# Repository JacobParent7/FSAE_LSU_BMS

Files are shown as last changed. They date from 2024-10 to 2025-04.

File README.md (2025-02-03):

# Motherboard
SENTRY



# Goal

Develop a distributed Battery Management System (BMS) for LSU FSAE's electric accumulator to be used in 2026 competition, targeting completion by May, 2025. All hardware and firmware development will be documented in this repository.

# Contact Info
### Motherboard Design
- Jacob Parent - jparen6@lsu.edu
### Daughterboard Design
- Parth Mistry - pmistr2@lsu.edu
- Modhy Alsahood - malsah1@lsu.edu

# FSAE BMS Design Log

## System Level Description 
BMS - MOBO drawio

## Orion BMS Thermistor Expansion Reverse Engineering
Blank diagram (1)

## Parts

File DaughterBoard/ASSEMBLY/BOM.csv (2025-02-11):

Reference | Value | Footprint | JLC PCB Part #
C201 | 10nF | GCM188R72A103KA37J:CAPC1608X90N | C2167085
C202,C208 | 0.1uF | GCM155R71A104KA55D:CAP_GCM15_1p05X0p55X0p55_MUR-L | C161163
C203,C204,C205,C207 | 1uF | C0603C105K8RACAUTO:CAPC18095_95N_KEM-L | C29936
C206 | 4.7uF | C2012X7R1A475M125AC:CAP_2012_TDK-L | C277499
C301,C302,C303,C304,C305,C306,C307,C308,C309,C310,C311,C312,C313,C314,C315,C316,C317,C318,C319,C320,C321,C322,C323,C324,C325,C326,C327,C328,C329,C330 | 0.47uF | GCM188R71C474KA55D:G-188_MUR-L | C161214
C601 | 0.22uF | GCM31MR72A224KA37L:G-31_MUR-L | C161277
C701,C702,C707,C708 | 2200pF | 1206J2K00222KXR (1):CAPC3216X160N | C107194
C703,C704,C705,C706 | 220pF | CL10B221JB8NNNC:CAP_CL10_SAM-L | C107081
D701,D702 | 24V | Package_TO_SOT_SMD:SOT-23 | C314266
F301,F302,F303,F304,F305,F306,F307,F308,F309,F310,F311,F323,F324,F325,F326 | 0438.250WRA | Fuse:Fuse_0603_1608Metric | C151137
F312,F313,F314,F315,F316,F317,F318,F319,F320,F321,F322,F327,F328,F329,F330 | 0686F1000-01 | 0686F1000-01:FUSC1608X60N | C136329
FL701,FL702 | 470uH | KiCad:744242471 | C488250
Q601 | ZXTN4004KTC | ZXTN4004KTC:ZXTN4004KTC | C157603
R201 | 30 | ERJ-3EKF30R0V:RC0603N_PAN-L | C403150
R301,R302,R303,R304,R305,R306,R307,R308,R309,R310,R311,R323,R324,R325,R326 | 7.5 | Resistor_SMD:R_1812_4532Metric | C5204035
R312,R313,R314,R315,R316,R317,R318,R319,R320,R321,R322,R327,R328,R329,R330 | 100 | Resistor_SMD:R_0603_1608Metric | C5123580
R601 | 100 | CRCW2010100RFKEF:RES_CRCW_2010-L | C305269
R602 | 200 | Resistor_SMD:R_2512_6332Metric | C2935248
R701,R702,R705,R706,R709,R710,R713,R714,R715,R716,R721,R722 | 0 | CRCW08050000Z0EAHP:RES_CRCW_0805_VIS-L | C844811
R703,R704,R719,R720 | 0 | RC0603JR-070RL:RC0603N_YAG-L | C95177
R707,R708,R717,R718 | 51 | CRCW060351R0JNEA:RC0603N_VIS-L | C844178
R711,R712 | 1k | ERJ-3EKF1001V:RC0603N_PAN-L | C2907002
U201 | BQ79614PAPRQ1 | BQ79614:QFP_4PAPRQ1_TEX-L | C3682338

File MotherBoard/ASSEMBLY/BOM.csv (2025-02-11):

Value | Reference | Footprint | JLCPCB Part #
100n | C203,C204,C206,C208,C210,C213,C215,C405,C406,C415,C416,C417,C418,C611,C612,C616,C617 | Capacitor_SMD:C_0402_1005Metric | C1525
100p | C503,C504,C505,C506 | Capacitor_SMD:C_0402_1005Metric | C1546
20p | C601,C602,C605,C606,C607,C608,C609,C610 | Capacitor_SMD:C_0402_1005Metric | C1554
RED | D501 | LED_SMD:LED_0603_1608Metric | C2286
Q_NMOS_GDS | Q704,Q705,Q706,Q708 | Package_TO_SOT_SMD:TO-263-2 | C2613
STM32F205RBTx | U201 | Package_QFP:LQFP-64_10x10mm_P0.5mm | C8364
1k | R201,R409,R410,R501 | Resistor_SMD:R_0402_1005Metric | C11702
Fuse | F701,F702,F703,F704 | Fuse:Fuse_1812_4532Metric | C12559
10u | C701,C702,C703,C704 | Capacitor_SMD:C_1206_3216Metric | C13585
16 Mhz | Y201 | Crystal:Crystal_SMD_3225-4Pin_3.2x2.5mm | C13738
0R | R203 | Resistor_SMD:R_0402_1005Metric | C17168
0R | R516,R517,R518,R519,R524,R525,R526,R527,R613,R614,R615,R616,R617,R618 | Resistor_SMD:R_0805_2012Metric | C17477
51 | R510,R511,R512,R513 | Resistor_SMD:R_1206_3216Metric | C18019
10u | C201,C216,C614,C619 | Capacitor_SMD:C_0603_1608Metric | C19702
220n | C507,C513 | Capacitor_SMD:C_0603_1608Metric | C21120
10n | L201 | Inductor_SMD:L_0402_1005Metric | C21585
D_Schottky | D405,D406 | Diode_SMD:D_SMA | C22452
499 | R502,R503,R504,R505 | Resistor_SMD:R_0603_1608Metric | C23065
22R | R204,R205,R206,R207,R210 | Resistor_SMD:R_0402_1005Metric | C25092
0R | R211 | Resistor_SMD:R_2512_6332Metric | C25469
100k | R402,R403,R405,R506,R515,R707,R708,R709,R712 | Resistor_SMD:R_0402_1005Metric | C25741
33k | R401,R404 | Resistor_SMD:R_0402_1005Metric | C25779
2.2k | R305 | Resistor_SMD:R_1206_3216Metric | C26038
2200p | C509,C510,C511,C512 | Capacitor_SMD:C_0805_2012Metric | C28260
1u | C409,C410,C411,C412,C413,C414 | Capacitor_SMD:C_0805_2012Metric | C28323
1u | C212,C214,C301,C613,C615,C618,C620 | Capacitor_SMD:C_0402_1005Metric | C29266
4.7u | C403,C404 | Capacitor_SMD:C_1206_3216Metric | C29823
22.1k | R406,R408 | Resistor_SMD:R_0402_1005Metric | C43473
22u | C419,C420,C421,C422,C423,C424 | Capacitor_SMD:C_0805_2012Metric | C45783
D_Zener | D401,D402 | Diode_SMD:D_SOD-323 | C46279
220n | C508 | Capacitor_SMD:C_0402_1005Metric | C47129
D_TVS | D201,D203,D204,D205,D206,D207,D208,D209,D301,D302,D303,D304,D305 | Diode_SMD:D_SOD-323 | C51450
10n | C211,C401,C402,C501,C502 | Capacitor_SMD:C_0402_1005Metric | C60133
2u2 | C207,C209 | Capacitor_SMD:C_0603_1608Metric | C99228
DM3AT-SF-PEJM5_40_ | J202 | SDIO:SD_CARD | C114218
100u | C407,C408 | Capacitor_SMD:CP_Elec_6.3x5.8 | C128464
10u | L403,L404 | Inductor_SMD:L_Sunlord_MWSA0603S | C132141
10p | C202,C205 | Capacitor_SMD:C_0402_1005Metric | C161520
3A | F401,F402 | Fuse:Fuse_1206_3216Metric | C182445
60.4 | R609,R610,R611,R612 | Resistor_SMD:R_1210_3225Metric | C230306
Fuse | F301,F302 | Fuse:Fuse_0805_2012Metric | C269104
4.7n | C603,C604 | Capacitor_SMD:C_0402_1005Metric | C281757
D_TVS | D403,D404,D407,D408 | Diode_SMD:D_SOD-123 | C353317
0R | R603,R604,R605,R606 | Resistor_SMD:R_1206_3216Metric | C473612
WE-SLM | L501,L502 | WE-SLM:WE-SLM | C488250
GREEN | D202,D409,D410 | LED_SMD:LED_0603_1608Metric | C511604
D_TVS | D502,D503,D504,D505 | Diode_SMD:D_SOD-323 | C668923
BQ79600PWRQ1 | IC501 | BQ79600:BQ79600 | C2869947
22R | R301,R302,R303,R304 | Resistor_SMD:R_1206_3216Metric | C2907457
10k | R202,R208,R209,R212,R507,R508,R509,R514,R601,R602,R607,R608,R701,R702,R703,R704,R705,R706,R710,R711 | Resistor_SMD:R_0402_1005Metric | C2930027
162k | R407 | Resistor_SMD:R_0402_1005Metric | C2998128
LMR51430 | U401,U402 | Package_TO_SOT_SMD:SOT-23-6 | C5210749
1.2u | L401,L402 | Inductor_SMD:L_Chilisin_BMRA00050530 | C5296375
PTCAN1462DRQ1 | U601,U602 | CAN1462:CAN1462 | C7399456
Q_NPN_BEC | Q701,Q702,Q703,Q707 | Package_TO_SOT_SMD:SOT-23 | C7420353
40V | D701,D702,D703,D704 | Diode_SMD:D_SOD-123 | C19077418

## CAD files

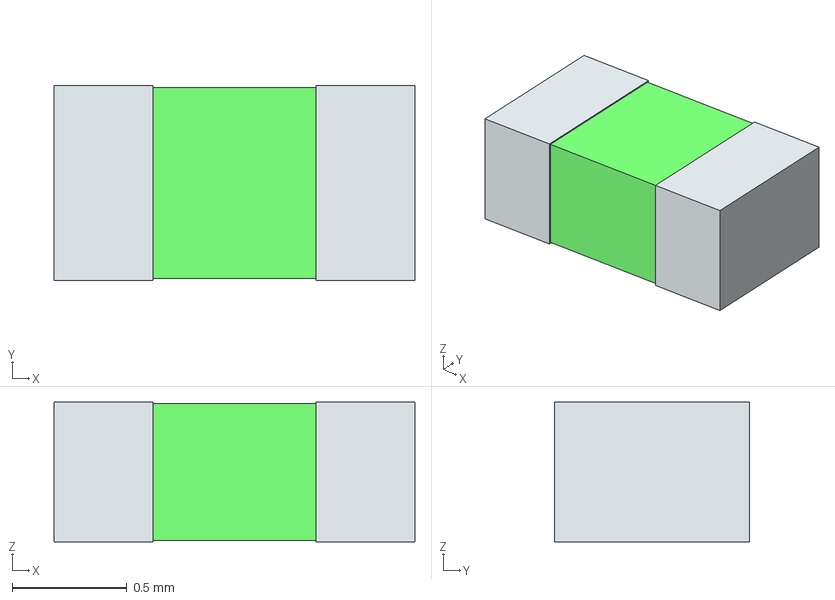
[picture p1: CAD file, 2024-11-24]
DaughterBoard/symbol-libs/models/0438.250WRASTEP/0438.250WRA.stp
1.57 x 0.85 x 0.61 mm
term1
term2

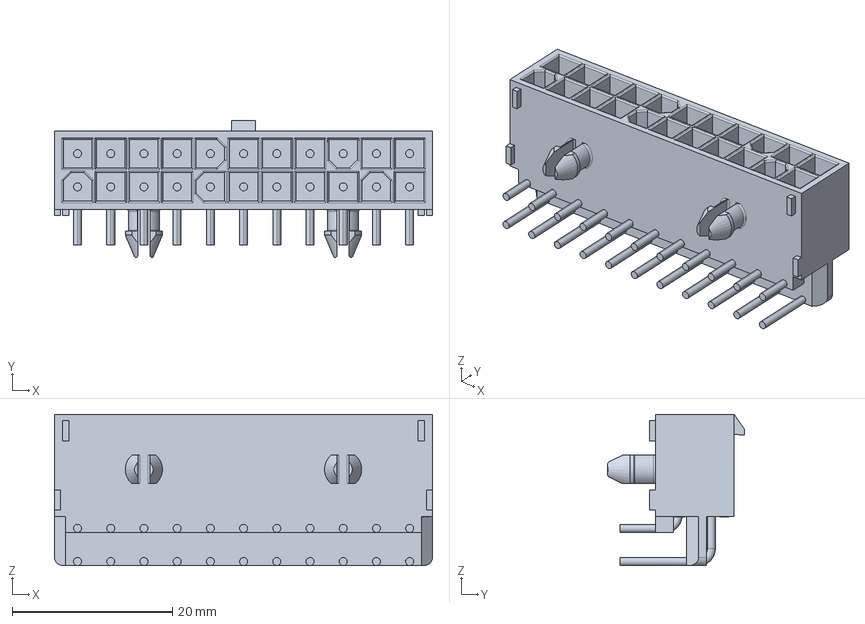
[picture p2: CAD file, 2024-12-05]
DaughterBoard/symbol-libs/models/c-1-794107-0-b-3d.stp
47.1 x 17.1 x 18.8 mm

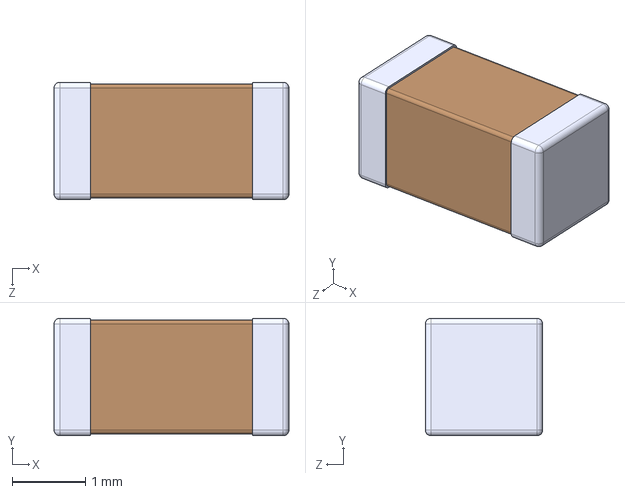
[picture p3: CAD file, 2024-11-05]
DaughterBoard/symbol-libs/symbols/1206J2K00222KXR (1)/1206J2K00222KXR.step
3.20 x 1.60 x 1.60 mm

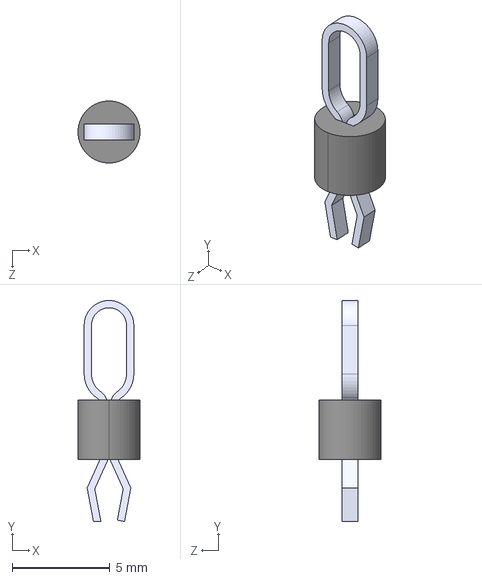
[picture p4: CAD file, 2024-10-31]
DaughterBoard/symbol-libs/symbols/5011 (1)/5011.step
3.17 x 11.3 x 3.17 mm

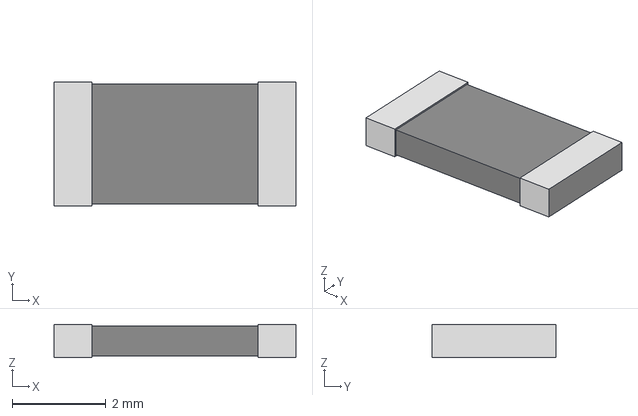
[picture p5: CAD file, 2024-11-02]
DaughterBoard/symbol-libs/symbols/CRCW2010100RFKEF/CRCW2010100RFKEF.step
5.16 x 2.64 x 0.711 mm

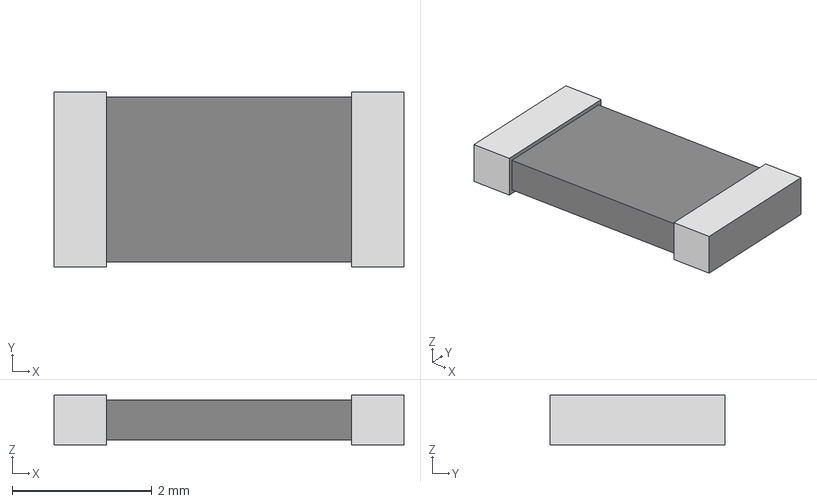
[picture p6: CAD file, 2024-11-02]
DaughterBoard/symbol-libs/symbols/CRCW2010200RFKEF/RC2010N_VIS.step
5.00 x 2.50 x 0.711 mm

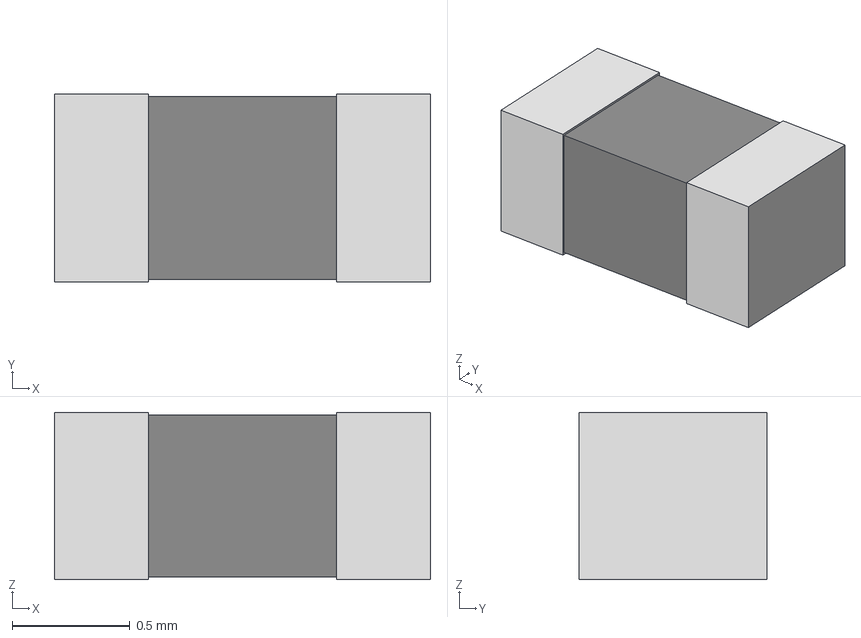
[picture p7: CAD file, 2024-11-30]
DaughterBoard/symbol-libs/symbols/ERJ_3EKF30R0V/ERJ-3EKF30R0V.step
1.60 x 0.8 x 0.711 mm

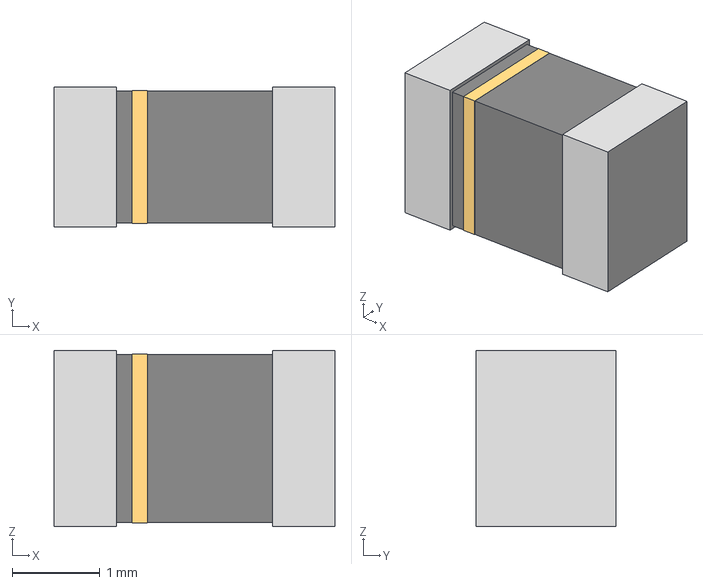
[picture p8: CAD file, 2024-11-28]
DaughterBoard/symbol-libs/symbols/G-31_MUR.step
3.20 x 1.60 x 2.01 mm

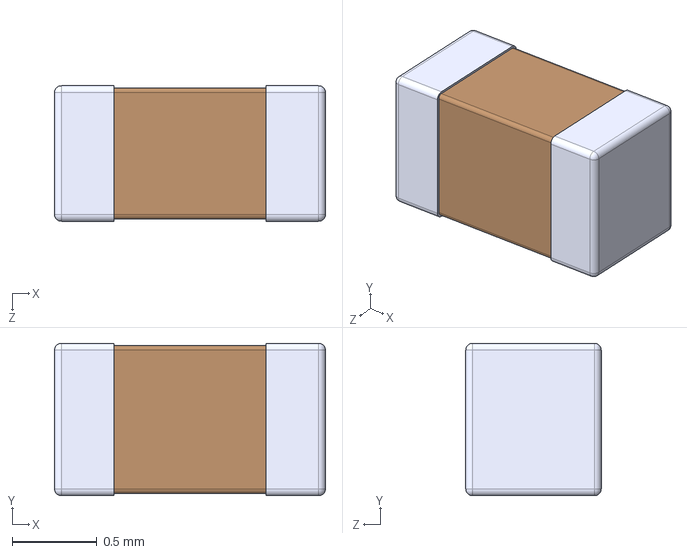
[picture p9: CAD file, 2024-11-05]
DaughterBoard/symbol-libs/symbols/GCM1885C1H101JA16J (1)/GCM1885C1H101JA16J.step
1.60 x 0.9 x 0.8 mm

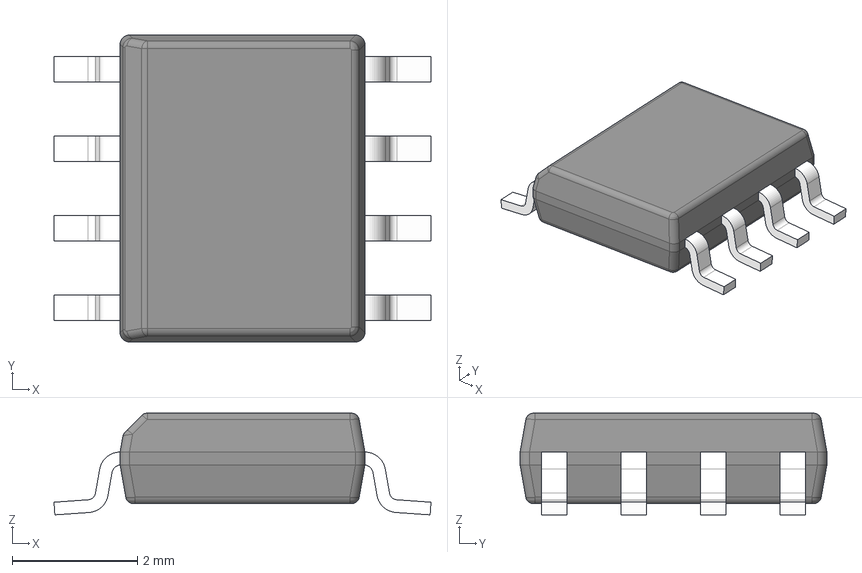
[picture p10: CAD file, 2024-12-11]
MotherBoard/Downloads/PTCAN1462/D0008A.stp
6.02 x 4.90 x 1.63 mm
BODY-SO
LEAD-D0008A x 8

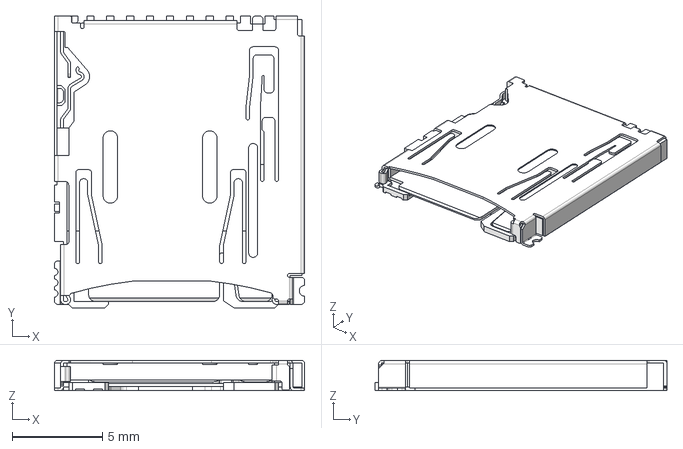
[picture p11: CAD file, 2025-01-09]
MotherBoard/Downloads/SD_CARD/DM3AT-SF-PEJM5_40_/3D/DM3AT-SF-PEJM5_40_.stp
13.8 x 16.2 x 1.68 mm

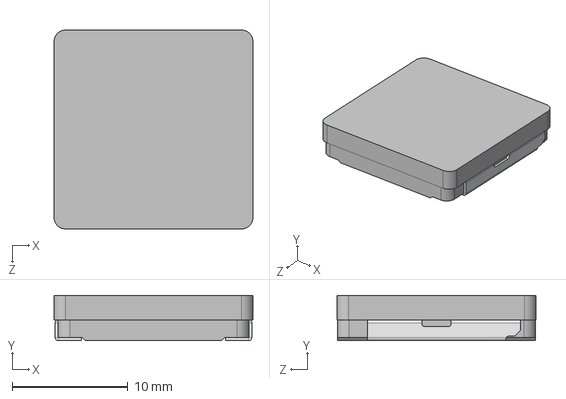
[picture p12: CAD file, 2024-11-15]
MotherBoard/Downloads/SW_Inductor/IHLP6767DZ.step
17.2 x 3.91 x 17.2 mm

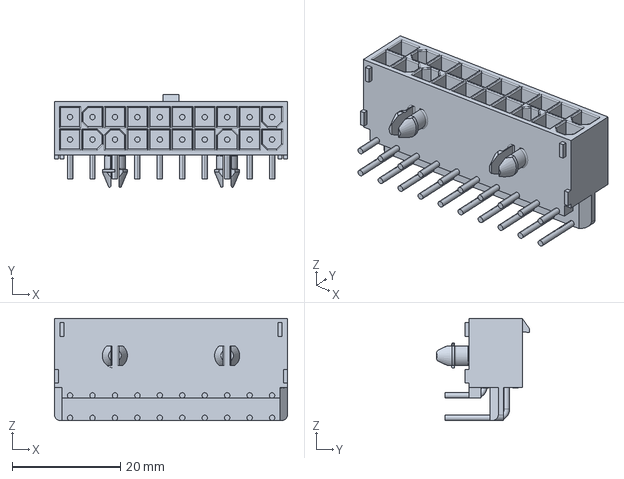
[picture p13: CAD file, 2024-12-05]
DaughterBoard/symbol-libs/models/c-1-794106-0-b-3d.stp
43.0 x 17.1 x 18.8 mm

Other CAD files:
DaughterBoard/symbol-libs/symbols/GCM188R72A103KA37J/GCM188R72A103KA37J.step
MotherBoard/Downloads/TP5012/5012.step
DaughterBoard/symbol-libs/models/0686F1000-01.STEP
DaughterBoard/symbol-libs/models/1.00kRC0603N_PAN.step
DaughterBoard/symbol-libs/models/705510038.stp
DaughterBoard/symbol-libs/models/705550019.stp
DaughterBoard/symbol-libs/models/CAP_2012_TDK.step
DaughterBoard/symbol-libs/models/CAP_CL10_SAM.step
DaughterBoard/symbol-libs/models/CAP_GCM15_1p05X0p55X0p55_MUR.step
DaughterBoard/symbol-libs/models/CCS_CCSTD_0603_L1.8W0.95T0.95B0.35.step
DaughterBoard/symbol-libs/models/CONN_PEC03SAAN_SUL.step
DaughterBoard/symbol-libs/models/CRCW060351R0JNEA.step
DaughterBoard/symbol-libs/models/CRCW08050000Z0EAHP.stp
DaughterBoard/symbol-libs/models/CRCW121010R0FKEAHP.step
DaughterBoard/symbol-libs/models/ERJ3EKF1001V.step
DaughterBoard/symbol-libs/models/G-31_MUR.step
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

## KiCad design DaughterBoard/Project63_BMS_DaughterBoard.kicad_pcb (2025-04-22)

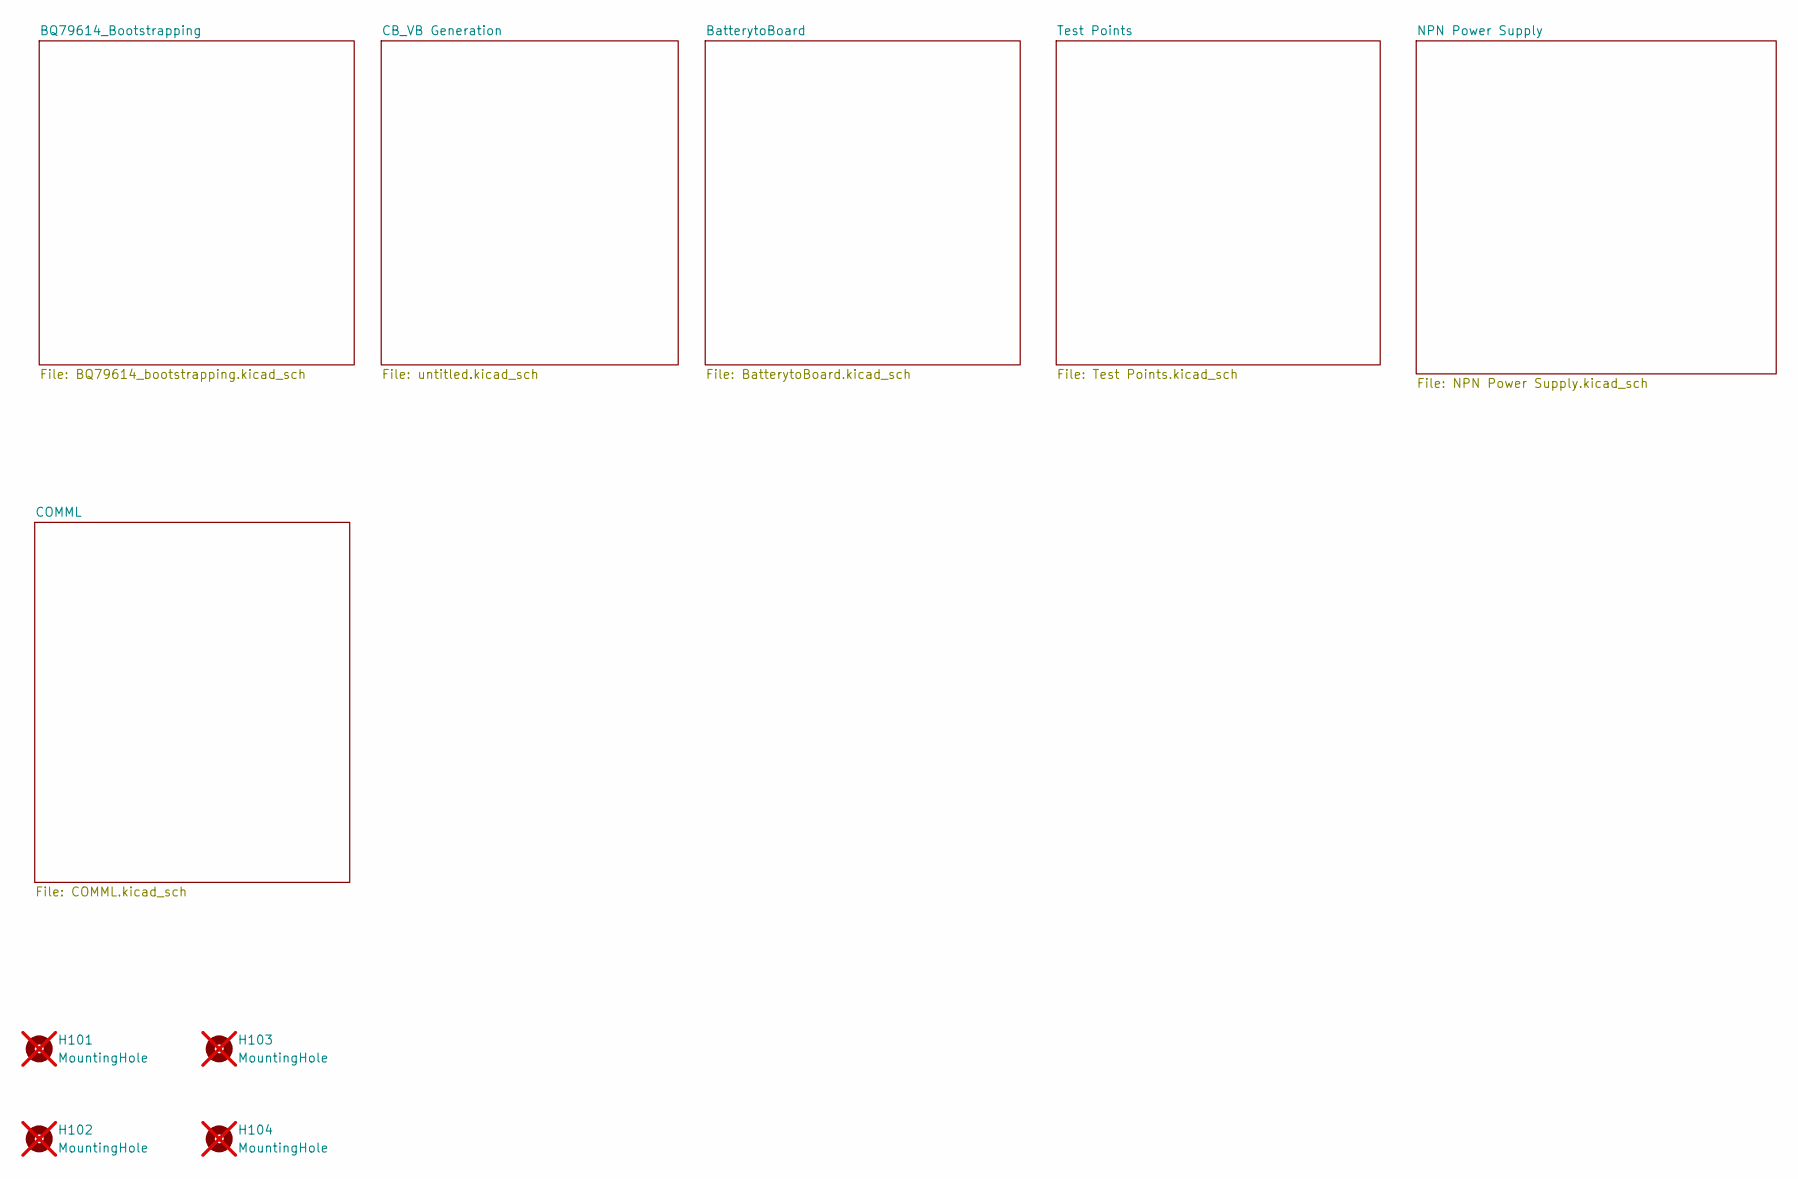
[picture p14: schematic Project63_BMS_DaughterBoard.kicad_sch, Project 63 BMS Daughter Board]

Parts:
H101, H102, H103, H104: MountingHole; MountingHole_3.2mm_M3; not fitted

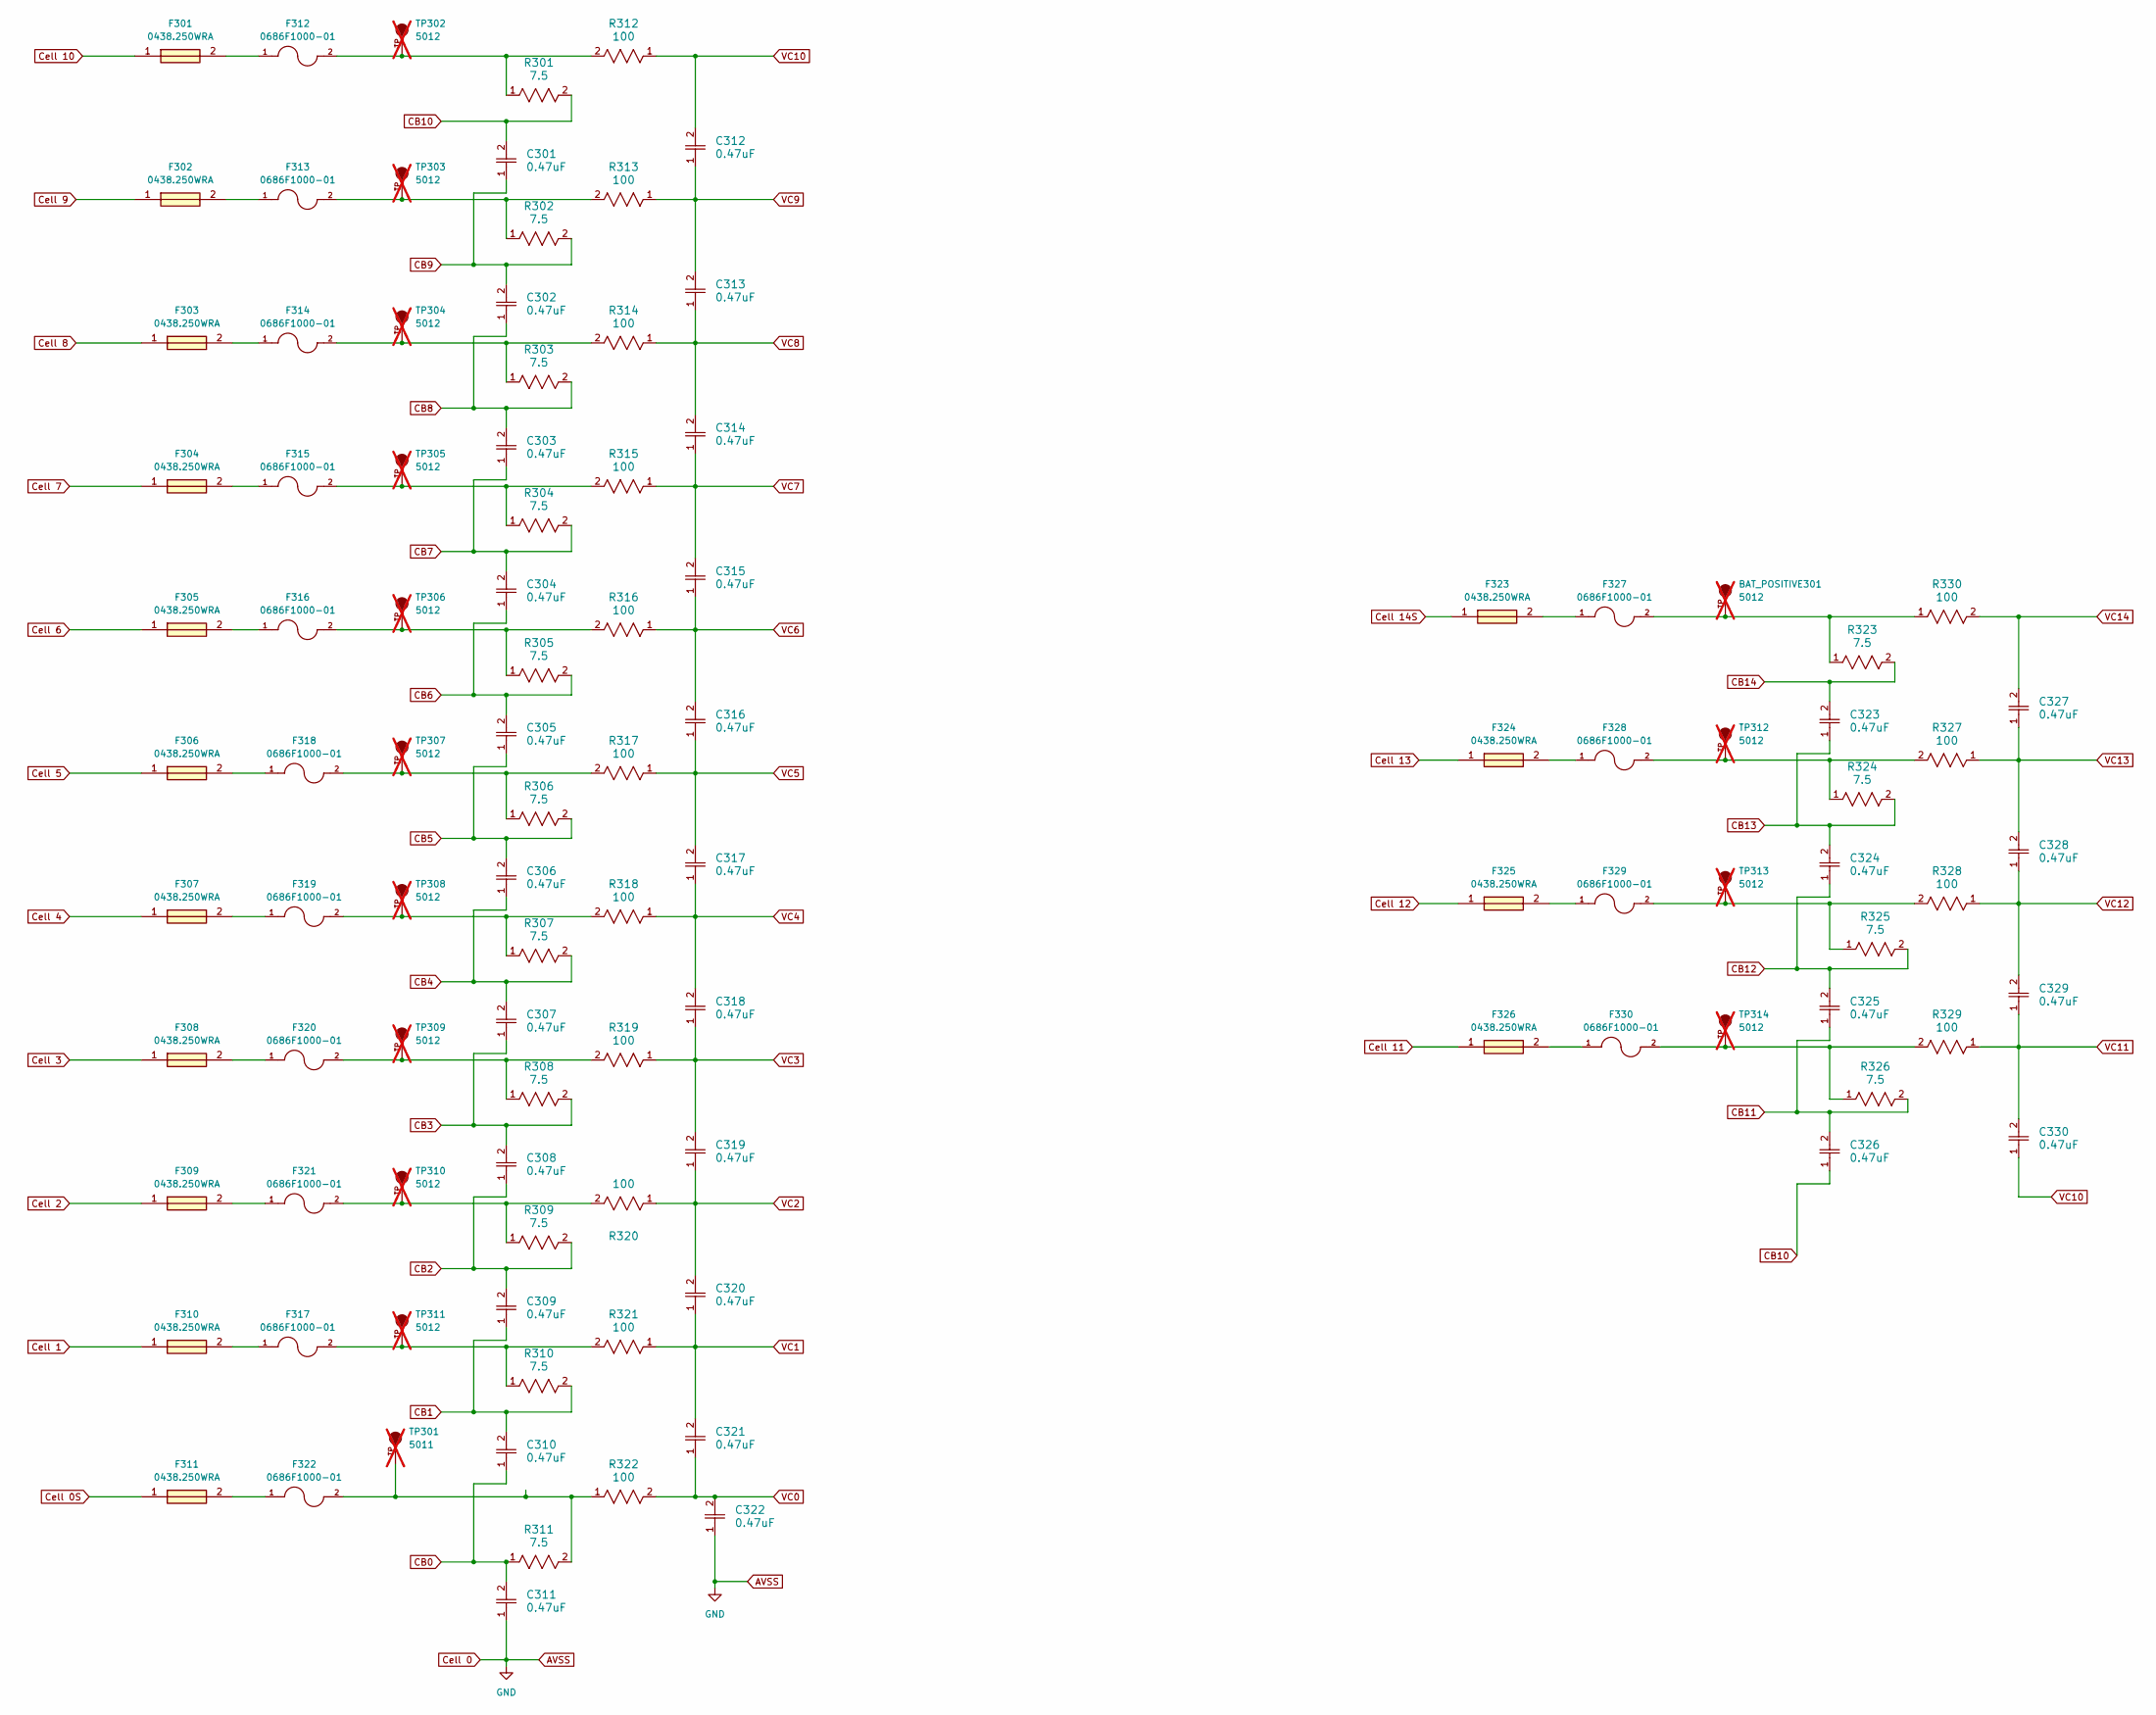
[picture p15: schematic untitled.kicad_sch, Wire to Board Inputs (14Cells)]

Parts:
BAT_POSITIVE301: 5012; TP_5012; PARTREV F; not fitted
C301, C302, C303, C304, C305, C306, C307, C308, C309, C310, C311, C312, C313, C314, C315, C316, C317, C318, C319, C320, C321, C322, C323, C324, C325, C326, C327, C328, C329, C330: 0.47uF; G-188_MUR-L; Manufacturer Part Number GCM188R71C474KA55D; JLC PCB Part # C161214
F301, F302, F303, F304, F305, F306, F307, F308, F309, F310, F311, F323, F324, F325, F326: 0438.250WRA; Fuse_0603_1608Metric; Manufacturer_Part_Number 0438.250WRA; Mouser Part Number 576-0438.250WRA
F312, F313, F314, F315, F316, F317, F318, F319, F320, F321, F322, F327, F328, F329, F330: 0686F1000-01; FUSC1608X60N; PARTREV Jan2019; JLC PCB Part # C136329
R301, R302, R303, R304, R305, R306, R307, R308, R309, R310, R311, R323, R324, R325, R326: 7.5; R_1812_4532Metric; Manufacturer Part Number FRC1812J7R5 TS; JLC PCB Part # C5204035
R312, R313, R314, R315, R316, R317, R318, R319, R320, R321, R322, R327, R328, R329, R330: 100; R_0603_1608Metric; Manufacturer Part Number HoAR0603-1/10W-100R-0.1%-TCR25; JLC PCB Part # C5123580
TP301: 5011; TP_5011; PARTREV F; not fitted
TP302, TP303, TP304, TP305, TP306, TP307, TP308, TP309, TP310, TP311, TP312, TP313, TP314: 5012; TP_5012; PARTREV F; not fitted

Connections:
AVSS: C311.1, C322.1; also elsewhere on the board
CB0: C310.1, C311.2, R311.1; also elsewhere on the board
CB1: C309.1, C310.2, R310.2; also elsewhere on the board
CB2: C308.1, C309.2, R309.2; also elsewhere on the board
CB3: C307.1, C308.2, R308.2; also elsewhere on the board
CB4: C306.1, C307.2, R307.2; also elsewhere on the board
CB5: C305.1, C306.2, R306.2; also elsewhere on the board
CB6: C304.1, C305.2, R305.2; also elsewhere on the board
CB7: C303.1, C304.2, R304.2; also elsewhere on the board
CB8: C302.1, C303.2, R303.2; also elsewhere on the board
CB9: C301.1, C302.2, R302.2; also elsewhere on the board
CB10: C301.2, C326.1, R301.2; also elsewhere on the board
CB11: C325.1, C326.2, R326.2; also elsewhere on the board
CB12: C324.1, C325.2, R325.2; also elsewhere on the board
CB13: C323.1, C324.2, R324.2; also elsewhere on the board
CB14: C323.2, R323.2; also elsewhere on the board
Cell 0S: F311.1; also elsewhere on the board
Cell 1: F310.1; also elsewhere on the board
Cell 2: F309.1; also elsewhere on the board
Cell 3: F308.1; also elsewhere on the board
Cell 4: F307.1; also elsewhere on the board
Cell 5: F306.1; also elsewhere on the board
Cell 6: F305.1; also elsewhere on the board
Cell 7: F304.1; also elsewhere on the board
Cell 8: F303.1; also elsewhere on the board
Cell 9: F302.1; also elsewhere on the board
Cell 10: F301.1; also elsewhere on the board
Cell 11: F326.1; also elsewhere on the board
Cell 12: F325.1; also elsewhere on the board
Cell 13: F324.1; also elsewhere on the board
Cell 14S: F323.1; also elsewhere on the board
unnamed: BAT_POSITIVE301.TP, F327.2, R323.1, R330.1
unnamed: F301.2, F312.1
unnamed: F302.2, F313.1
unnamed: F303.2, F314.1
unnamed: F304.2, F315.1
unnamed: F305.2, F316.1
unnamed: F306.2, F318.1
unnamed: F307.2, F319.1
unnamed: F308.2, F320.1
unnamed: F309.2, F321.1
unnamed: F310.2, F317.1
unnamed: F311.2, F322.1
unnamed: F312.2, R301.1, R312.2, TP302.TP
unnamed: F313.2, R302.1, R313.2, TP303.TP
unnamed: F314.2, R303.1, R314.2, TP304.TP
unnamed: F315.2, R304.1, R315.2, TP305.TP
unnamed: F316.2, R305.1, R316.2, TP306.TP
unnamed: F317.2, R310.1, R321.2, TP311.TP
unnamed: F318.2, R306.1, R317.2, TP307.TP
unnamed: F319.2, R307.1, R318.2, TP308.TP
unnamed: F320.2, R308.1, R319.2, TP309.TP
unnamed: F321.2, R309.1, R320.2, TP310.TP
unnamed: F322.2, R311.2, R322.1, TP301.TP
unnamed: F323.2, F327.1
unnamed: F324.2, F328.1
unnamed: F325.2, F329.1
unnamed: F326.2, F330.1
unnamed: F328.2, R324.1, R327.2, TP312.TP
unnamed: F329.2, R325.1, R328.2, TP313.TP
unnamed: F330.2, R326.1, R329.2, TP314.TP
VC0: C321.1, C322.2, R322.2; also elsewhere on the board
VC1: C320.1, C321.2, R321.1; also elsewhere on the board
VC2: C319.1, C320.2, R320.1; also elsewhere on the board
VC3: C318.1, C319.2, R319.1; also elsewhere on the board
VC4: C317.1, C318.2, R318.1; also elsewhere on the board
VC5: C316.1, C317.2, R317.1; also elsewhere on the board
VC6: C315.1, C316.2, R316.1; also elsewhere on the board
VC7: C314.1, C315.2, R315.1; also elsewhere on the board
VC8: C313.1, C314.2, R314.1; also elsewhere on the board
VC9: C312.1, C313.2, R313.1; also elsewhere on the board
VC10: C312.2, C330.1, R312.1; also elsewhere on the board
VC11: C329.1, C330.2, R329.1; also elsewhere on the board
VC12: C328.1, C329.2, R328.1; also elsewhere on the board
VC13: C327.1, C328.2, R327.1; also elsewhere on the board
VC14: C327.2, R330.2; also elsewhere on the board

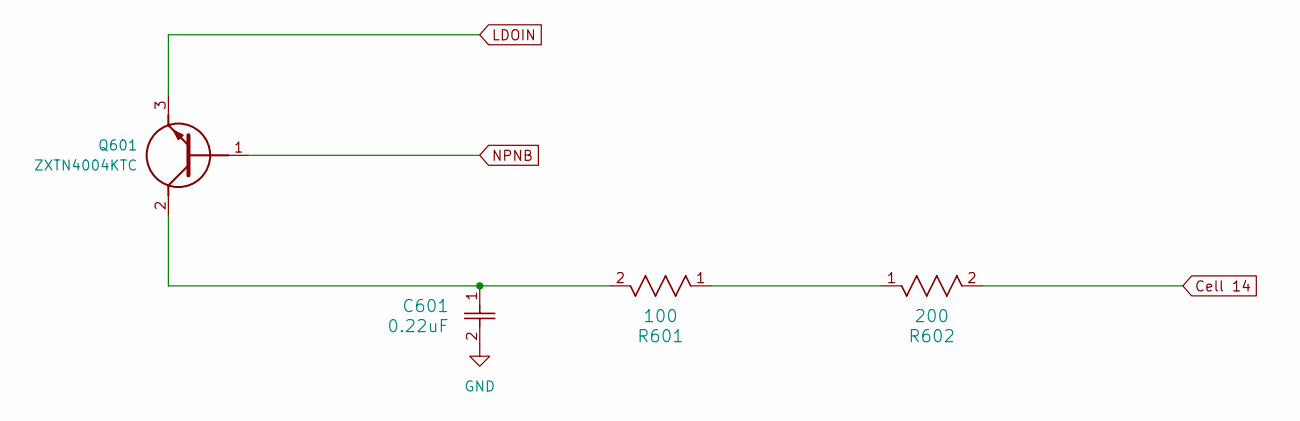
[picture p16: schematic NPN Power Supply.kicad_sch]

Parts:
C601: 0.22uF; G-31_MUR-L; Manufacturer Part Number GCM31MR72A224KA37L; JLC PCB Part # C161277
Q601: ZXTN4004KTC; Mouser Part Number 621-ZXTN4004KTC
R601: 100; RES_CRCW_2010-L; Manufacturer Part Number WF20P1000FTL; JLC PCB Part # C305269
R602: 200; R_2512_6332Metric; Manufacturer Part Number RC2512JK-07200RL; JLC PCB Part # C2935248

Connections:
AVSS: C601.2; also elsewhere on the board
BAT: R602.2; also elsewhere on the board
LDOIN: Q601.3 (E); also elsewhere on the board
NPNB: Q601.1 (B); also elsewhere on the board
unnamed: C601.1, Q601.2 (C), R601.2
unnamed: R601.1, R602.1

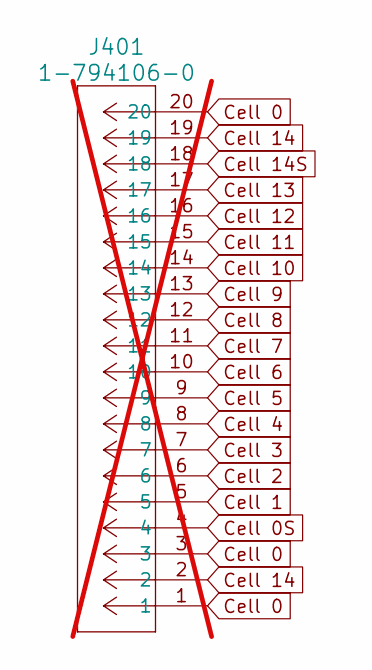
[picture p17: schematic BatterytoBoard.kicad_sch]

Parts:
J401: 1-794106-0; CON20_2X10_P4.14MM_RAMNL_TYC; not fitted

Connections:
AVSS: J401.1, J401.3, J401.20; also elsewhere on the board
BAT: J401.2, J401.19; also elsewhere on the board
Cell 0S: J401.4; also elsewhere on the board
Cell 1: J401.5; also elsewhere on the board
Cell 2: J401.6; also elsewhere on the board
Cell 3: J401.7; also elsewhere on the board
Cell 4: J401.8; also elsewhere on the board
Cell 5: J401.9; also elsewhere on the board
Cell 6: J401.10; also elsewhere on the board
Cell 7: J401.11; also elsewhere on the board
Cell 8: J401.12; also elsewhere on the board
Cell 9: J401.13; also elsewhere on the board
Cell 10: J401.14; also elsewhere on the board
Cell 11: J401.15; also elsewhere on the board
Cell 12: J401.16; also elsewhere on the board
Cell 13: J401.17; also elsewhere on the board
Cell 14S: J401.18; also elsewhere on the board

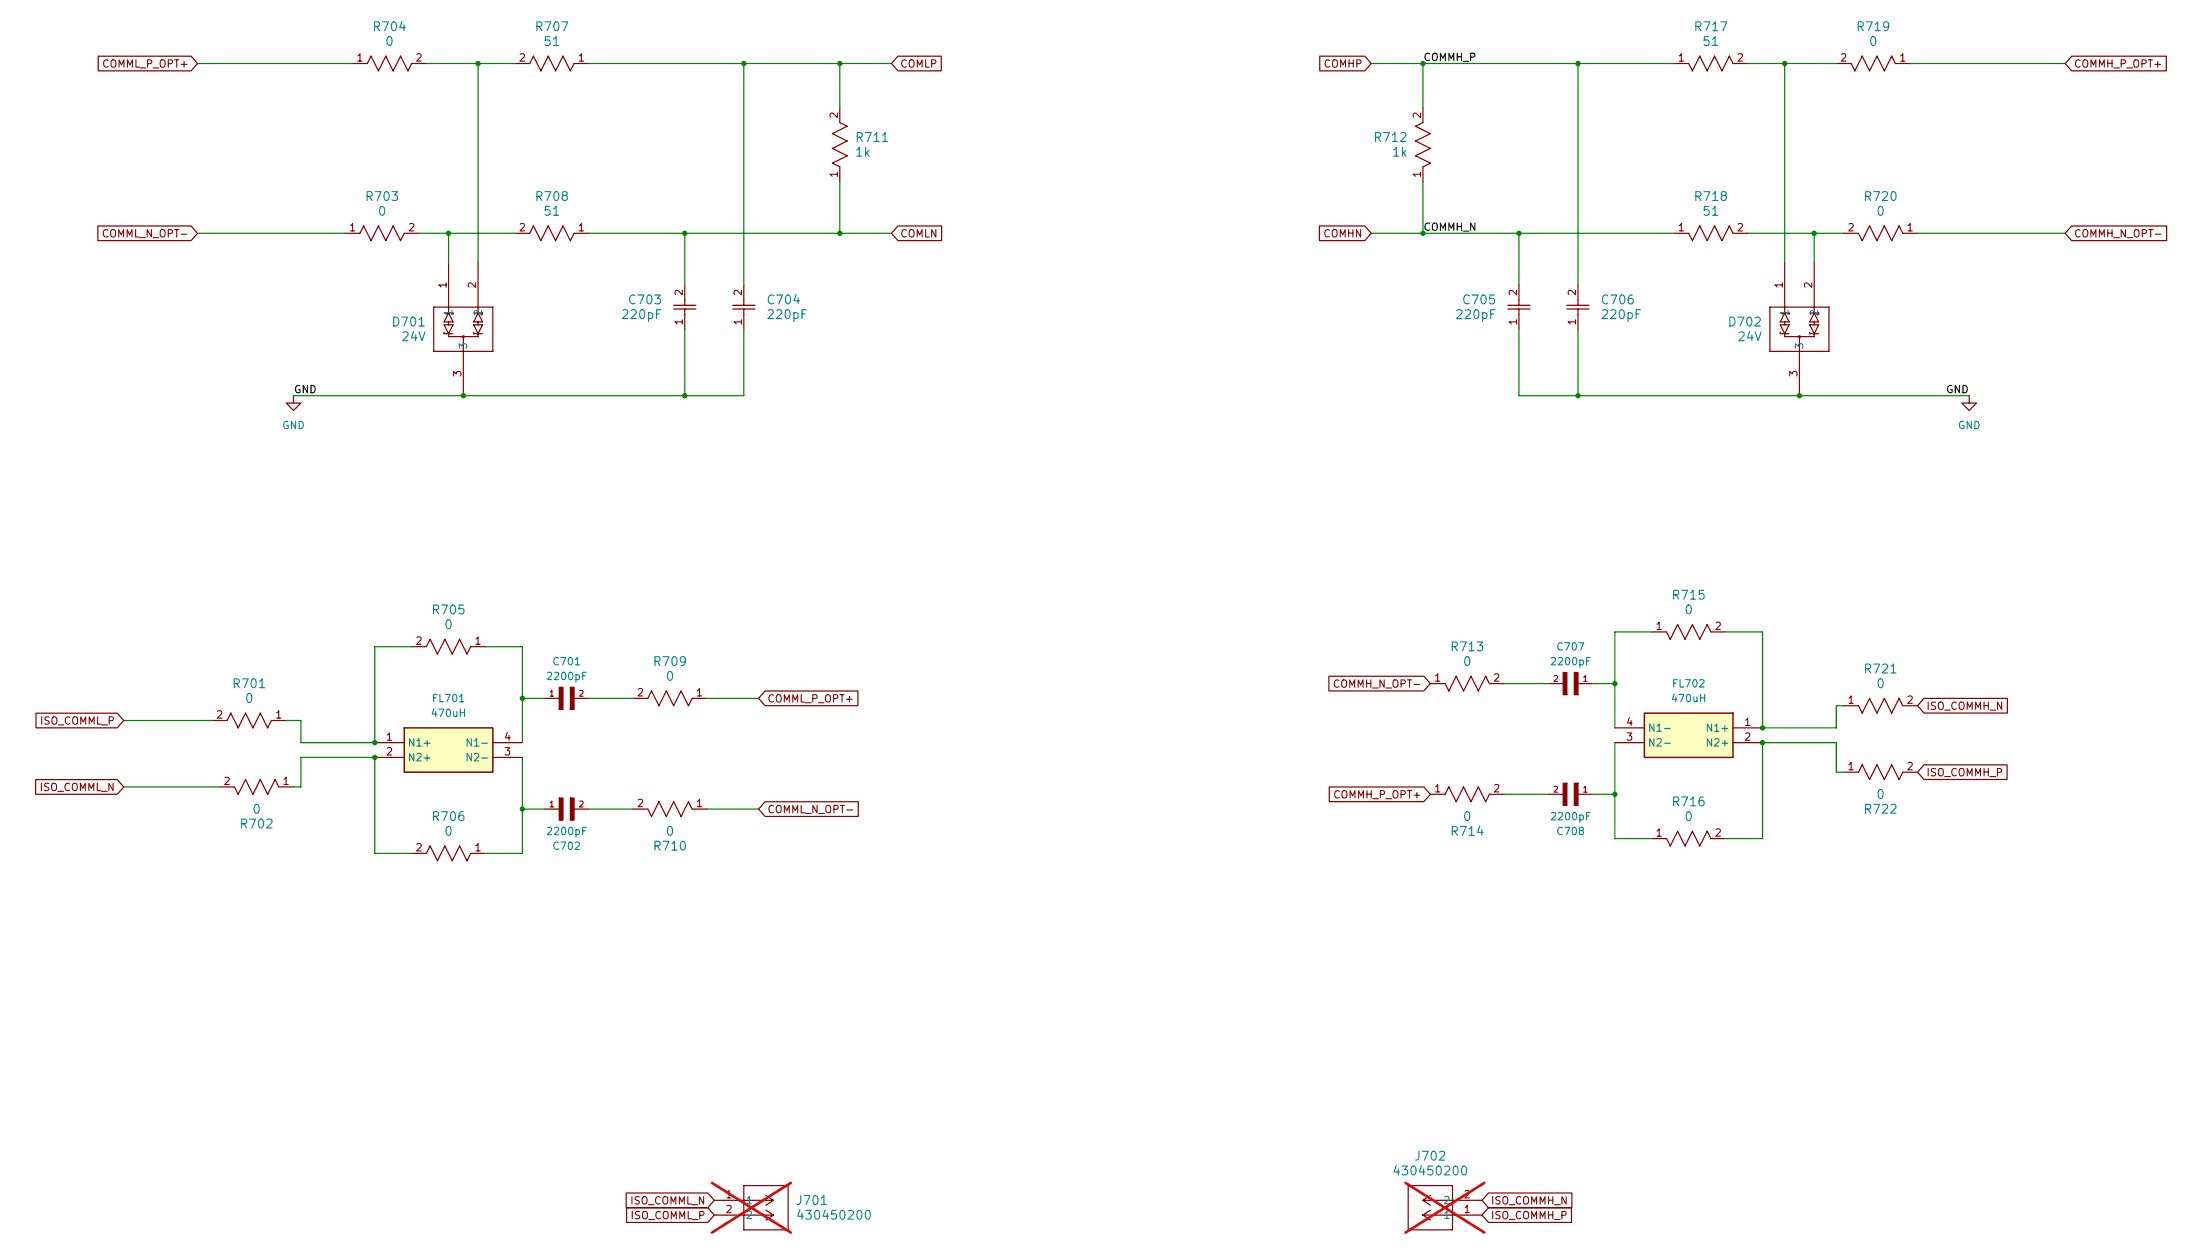
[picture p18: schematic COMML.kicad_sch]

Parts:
C701, C702, C707, C708: 2200pF; CAPC3216X160N; Manufacturer Part Number CC1206KKX7RCBB222; JLC PCB Part # C107194
C703, C704, C705, C706: 220pF; CAP_CL10_SAM-L; Manufacturer Part Number CC0603KRX7R9BB221; JLC PCB Part # C107081
D701, D702: 24V; SOT-23; Manufacturer Part Number PESD24VL2BTN; JLC PCB Part # C314266
FL701, FL702: 470uH; 744242471; Mouser Part Number 710-744242471
J701, J702: 430450200; CON_430450200_MOL; not fitted
R701, R702, R705, R706, R709, R710, R713, R714, R715, R716, R721, R722: 0; RES_CRCW_0805_VIS-L; Manufacturer Part Number CRCW08050000Z0EAHP; JLC PCB Part # C844811
R703, R704, R719, R720: 0; RC0603N_YAG-L; Manufacturer Part Number RC0603JR-070RL; JLC PCB Part # C95177
R707, R708, R717, R718: 51; RC0603N_VIS-L; Manufacturer Part Number CRCW060351R0JNEA; JLC PCB Part # C844178
R711, R712: 1k; RC0603N_PAN-L; Manufacturer Part Number FRC0603F1001TS; JLC PCB Part # C2907002

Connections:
AVSS: C703.1, C704.1, C705.1, C706.1, D701.3, D702.3; also elsewhere on the board
COMHN: C705.2, R712.1, R718.1; also elsewhere on the board
COMHP: C706.2, R712.2, R717.1; also elsewhere on the board
COMLN: C703.2, R708.1, R711.1; also elsewhere on the board
COMLP: C704.2, R707.1, R711.2; also elsewhere on the board
COMMH_N_OPT-: R713.1, R720.1
COMMH_P_OPT+: R714.1, R719.1
COMML_N_OPT-: R703.1, R710.1
COMML_P_OPT+: R704.1, R709.1
ISO_COMMH_N: J702.2, R721.2
ISO_COMMH_P: J702.1, R722.2
ISO_COMML_N: J701.1, R702.2
ISO_COMML_P: J701.2, R701.2
unnamed: C701.2, R709.2
unnamed: C702.2, R710.2
unnamed: C707.2, R713.2
unnamed: C708.2, R714.2
unnamed: D701.1, R703.2, R708.2
unnamed: D701.2, R704.2, R707.2
unnamed: D702.1, R717.2, R719.2
unnamed: D702.2, R718.2, R720.2
unnamed: FL701.1 (N1+), R701.1, R705.2
unnamed: C701.1, FL701.4 (N1-), R705.1
unnamed: FL701.2 (N2+), R702.1, R706.2
unnamed: C702.1, FL701.3 (N2-), R706.1
unnamed: FL702.1 (N1+), R715.2, R721.1
unnamed: C707.1, FL702.4 (N1-), R715.1
unnamed: FL702.2 (N2+), R716.2, R722.1
unnamed: C708.1, FL702.3 (N2-), R716.1

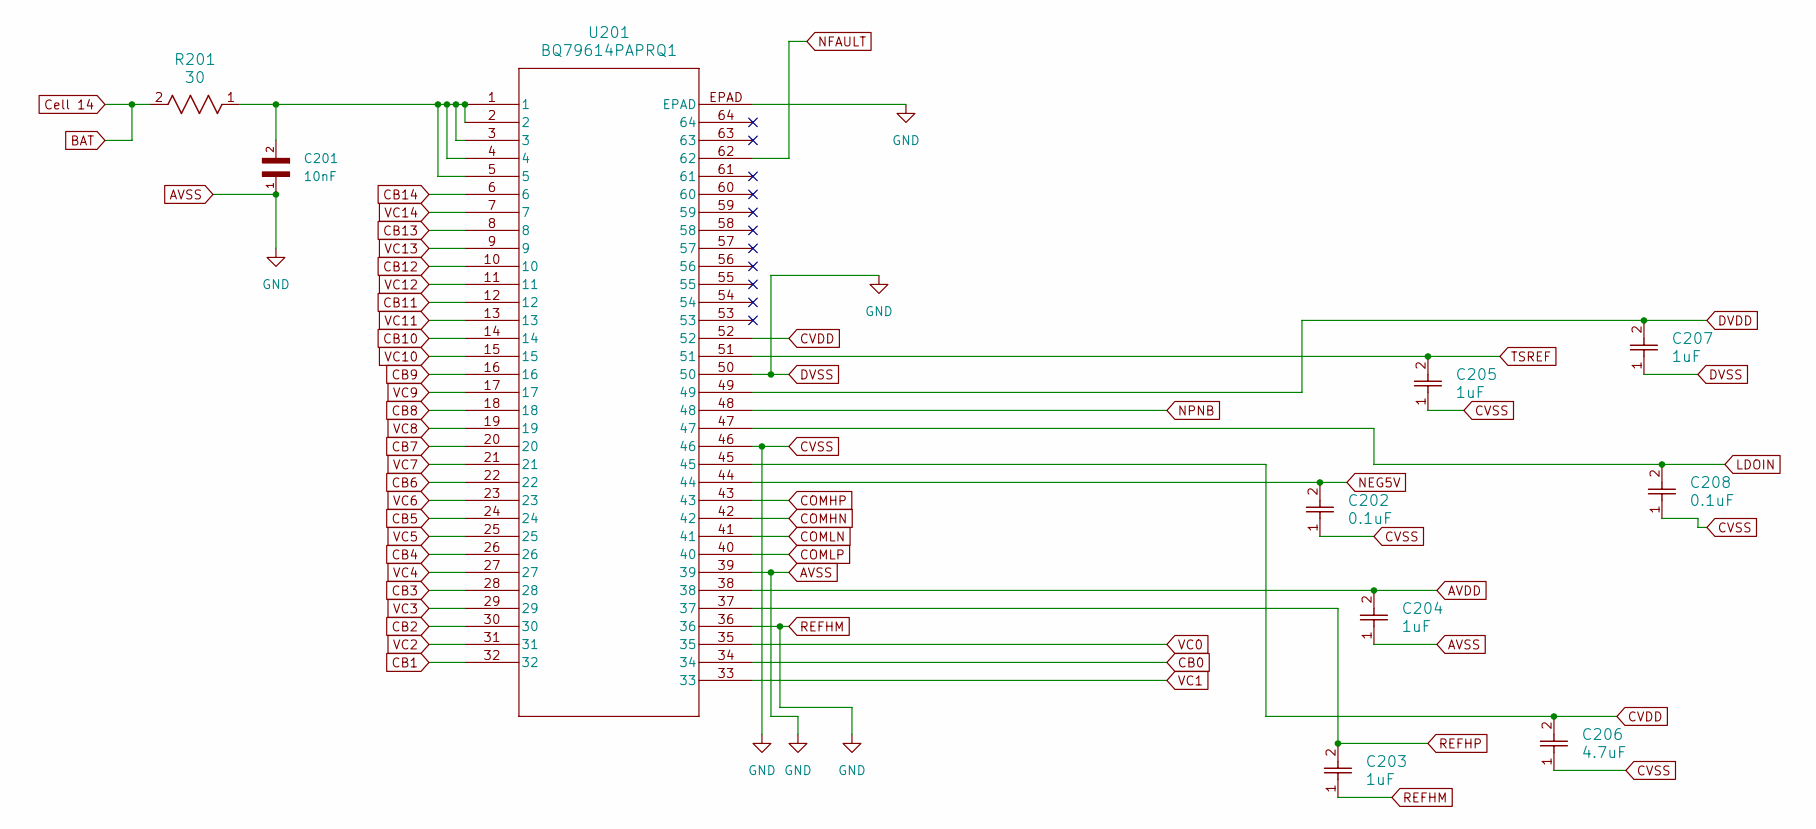
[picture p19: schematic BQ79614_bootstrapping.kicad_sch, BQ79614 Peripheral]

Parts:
C201: 10nF; CAPC1608X90N; Manufacturer Part Number GCM188R72A103KA37J; JLC PCB Part # C2167085
C202, C208: 0.1uF; CAP_GCM15_1p05X0p55X0p55_MUR-L; Manufacturer Part Number GCM155R71A104KA55D; JLC PCB Part # C161163
C203, C204, C205, C207: 1uF; CAPC18095_95N_KEM-L; Manufacturer Part Number CL10B105KA8NNNC; JLC PCB Part # C29936
C206: 4.7uF; CAP_2012_TDK-L; Manufacturer Part Number CC0805KKX7R7BB475; JLC PCB Part # C277499
R201: 30; RC0603N_PAN-L; Manufacturer Part Number ERJ-3EKF30R0V; JLC PCB Part # C403150
U201: BQ79614PAPRQ1; QFP_4PAPRQ1_TEX-L; Manufacturer Part Number BQ79616PAPRQ1; JLC PCB Part # C3682338

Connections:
AVDD: C204.2, U201.38; also elsewhere on the board
AVSS: C201.1, C202.1, C203.1, C204.1, C205.1, C206.1, C207.1, C208.1, U201.36, U201.39, U201.46, U201.50, U201.EPAD; also elsewhere on the board
BAT: R201.2; also elsewhere on the board
CB0: U201.34; also elsewhere on the board
CB1: U201.32; also elsewhere on the board
CB2: U201.30; also elsewhere on the board
CB3: U201.28; also elsewhere on the board
CB4: U201.26; also elsewhere on the board
CB5: U201.24; also elsewhere on the board
CB6: U201.22; also elsewhere on the board
CB7: U201.20; also elsewhere on the board
CB8: U201.18; also elsewhere on the board
CB9: U201.16; also elsewhere on the board
CB10: U201.14; also elsewhere on the board
CB11: U201.12; also elsewhere on the board
CB12: U201.10; also elsewhere on the board
CB13: U201.8; also elsewhere on the board
CB14: U201.6; also elsewhere on the board
COMHN: U201.42; also elsewhere on the board
COMHP: U201.43; also elsewhere on the board
COMLN: U201.41; also elsewhere on the board
COMLP: U201.40; also elsewhere on the board
CVDD: C206.2, U201.45, U201.52; also elsewhere on the board
DVDD: C207.2, U201.49; also elsewhere on the board
LDOIN: C208.2, U201.47; also elsewhere on the board
NEG5V: C202.2, U201.44; also elsewhere on the board
NFAULT: U201.62; also elsewhere on the board
NPNB: U201.48; also elsewhere on the board
unnamed: C201.2, R201.1, U201.1, U201.2, U201.3, U201.4, U201.5
REFHP: C203.2, U201.37; also elsewhere on the board
TSREF: C205.2, U201.51; also elsewhere on the board
VC0: U201.35; also elsewhere on the board
VC1: U201.33; also elsewhere on the board
VC2: U201.31; also elsewhere on the board
VC3: U201.29; also elsewhere on the board
VC4: U201.27; also elsewhere on the board
VC5: U201.25; also elsewhere on the board
VC6: U201.23; also elsewhere on the board
VC7: U201.21; also elsewhere on the board
VC8: U201.19; also elsewhere on the board
VC9: U201.17; also elsewhere on the board
VC10: U201.15; also elsewhere on the board
VC11: U201.13; also elsewhere on the board
VC12: U201.11; also elsewhere on the board
VC13: U201.9; also elsewhere on the board
VC14: U201.7; also elsewhere on the board

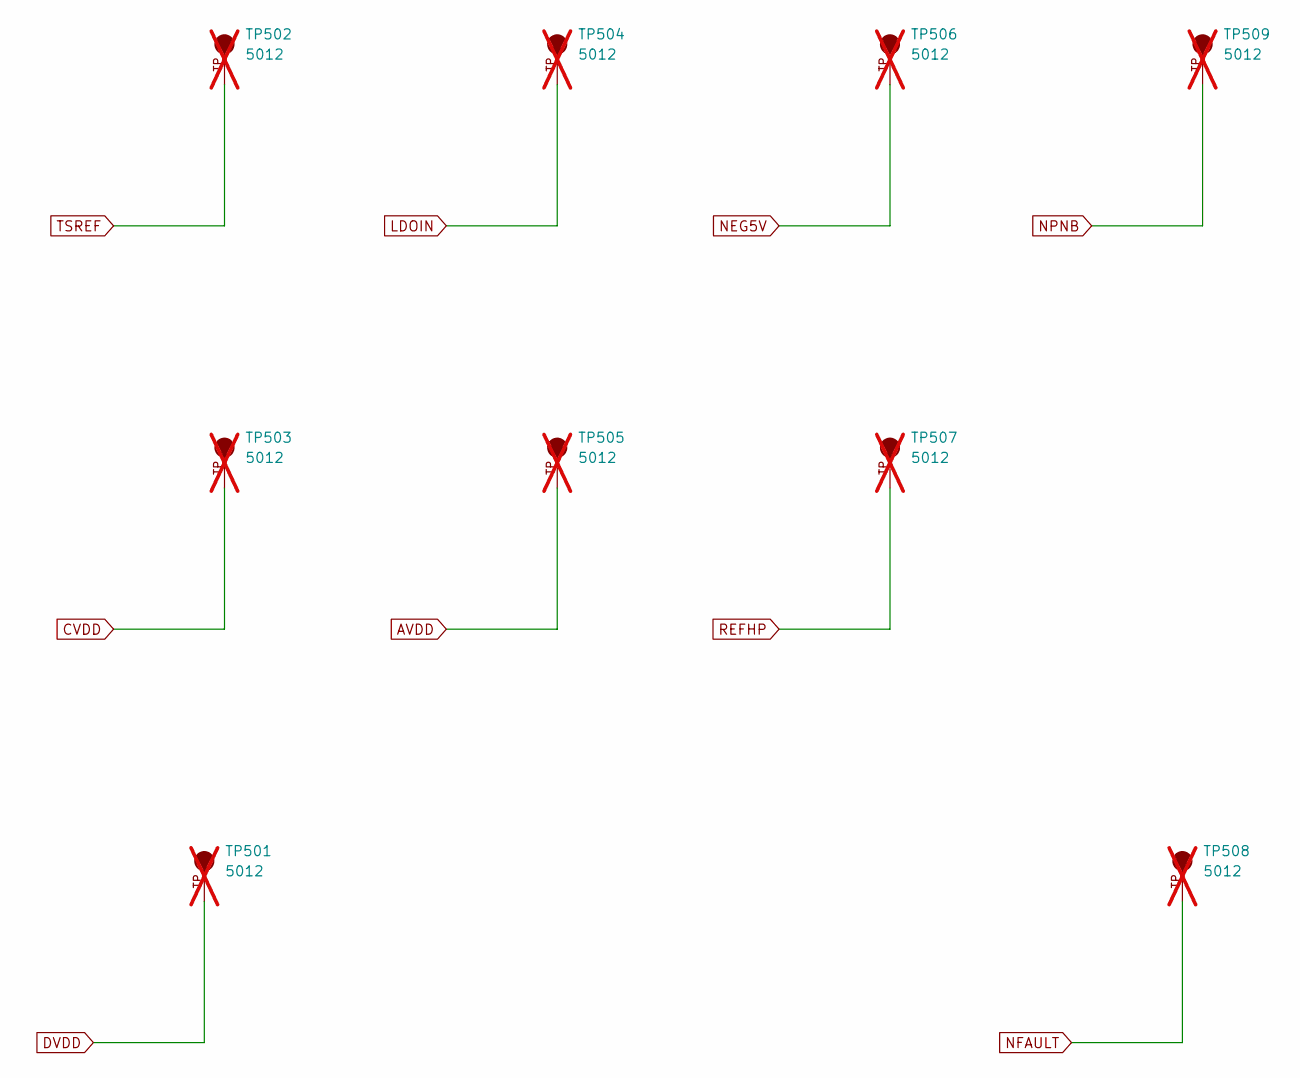
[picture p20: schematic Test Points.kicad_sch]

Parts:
TP501, TP502, TP503, TP504, TP505, TP506, TP507, TP508, TP509: 5012; TP_5012; PARTREV F; not fitted

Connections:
AVDD: TP505.TP; also elsewhere on the board
CVDD: TP503.TP; also elsewhere on the board
DVDD: TP501.TP; also elsewhere on the board
LDOIN: TP504.TP; also elsewhere on the board
NEG5V: TP506.TP; also elsewhere on the board
NFAULT: TP508.TP; also elsewhere on the board
NPNB: TP509.TP; also elsewhere on the board
REFHP: TP507.TP; also elsewhere on the board
TSREF: TP502.TP; also elsewhere on the board

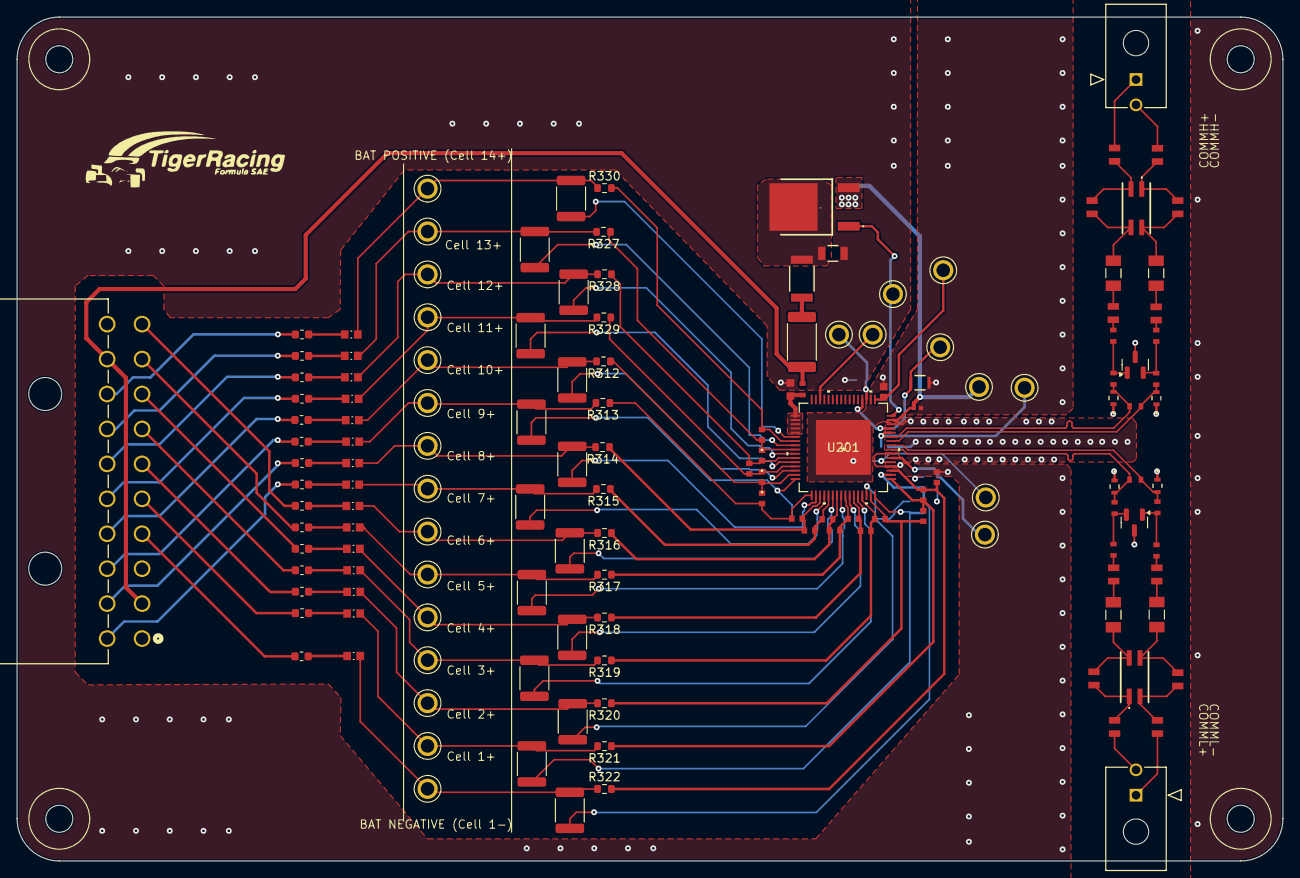
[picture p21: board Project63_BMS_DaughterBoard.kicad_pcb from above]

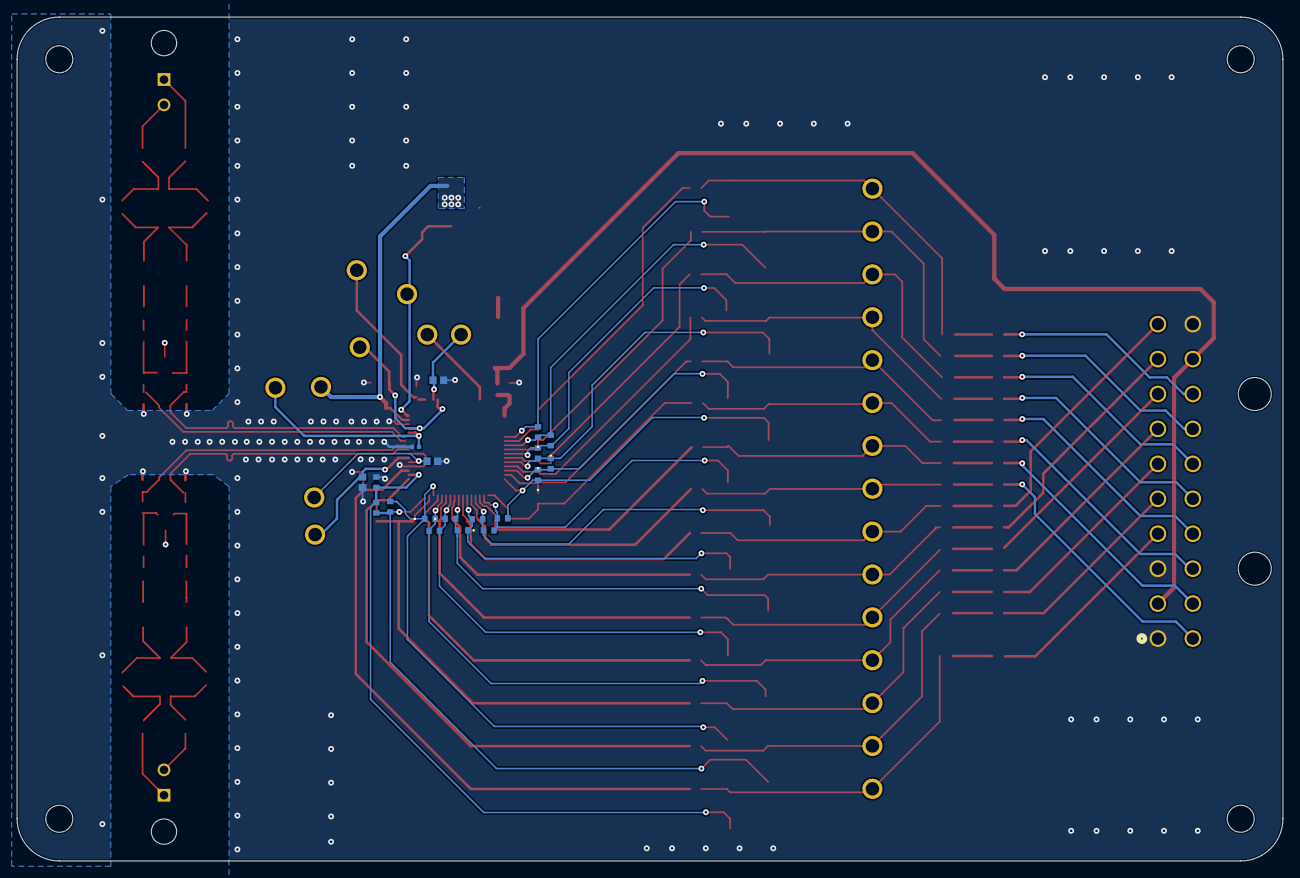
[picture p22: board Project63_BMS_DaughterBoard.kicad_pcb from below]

Board: 4 copper layers, 150.0 x 100.0 mm, 169 parts (19 on the bottom side), 117 nets.

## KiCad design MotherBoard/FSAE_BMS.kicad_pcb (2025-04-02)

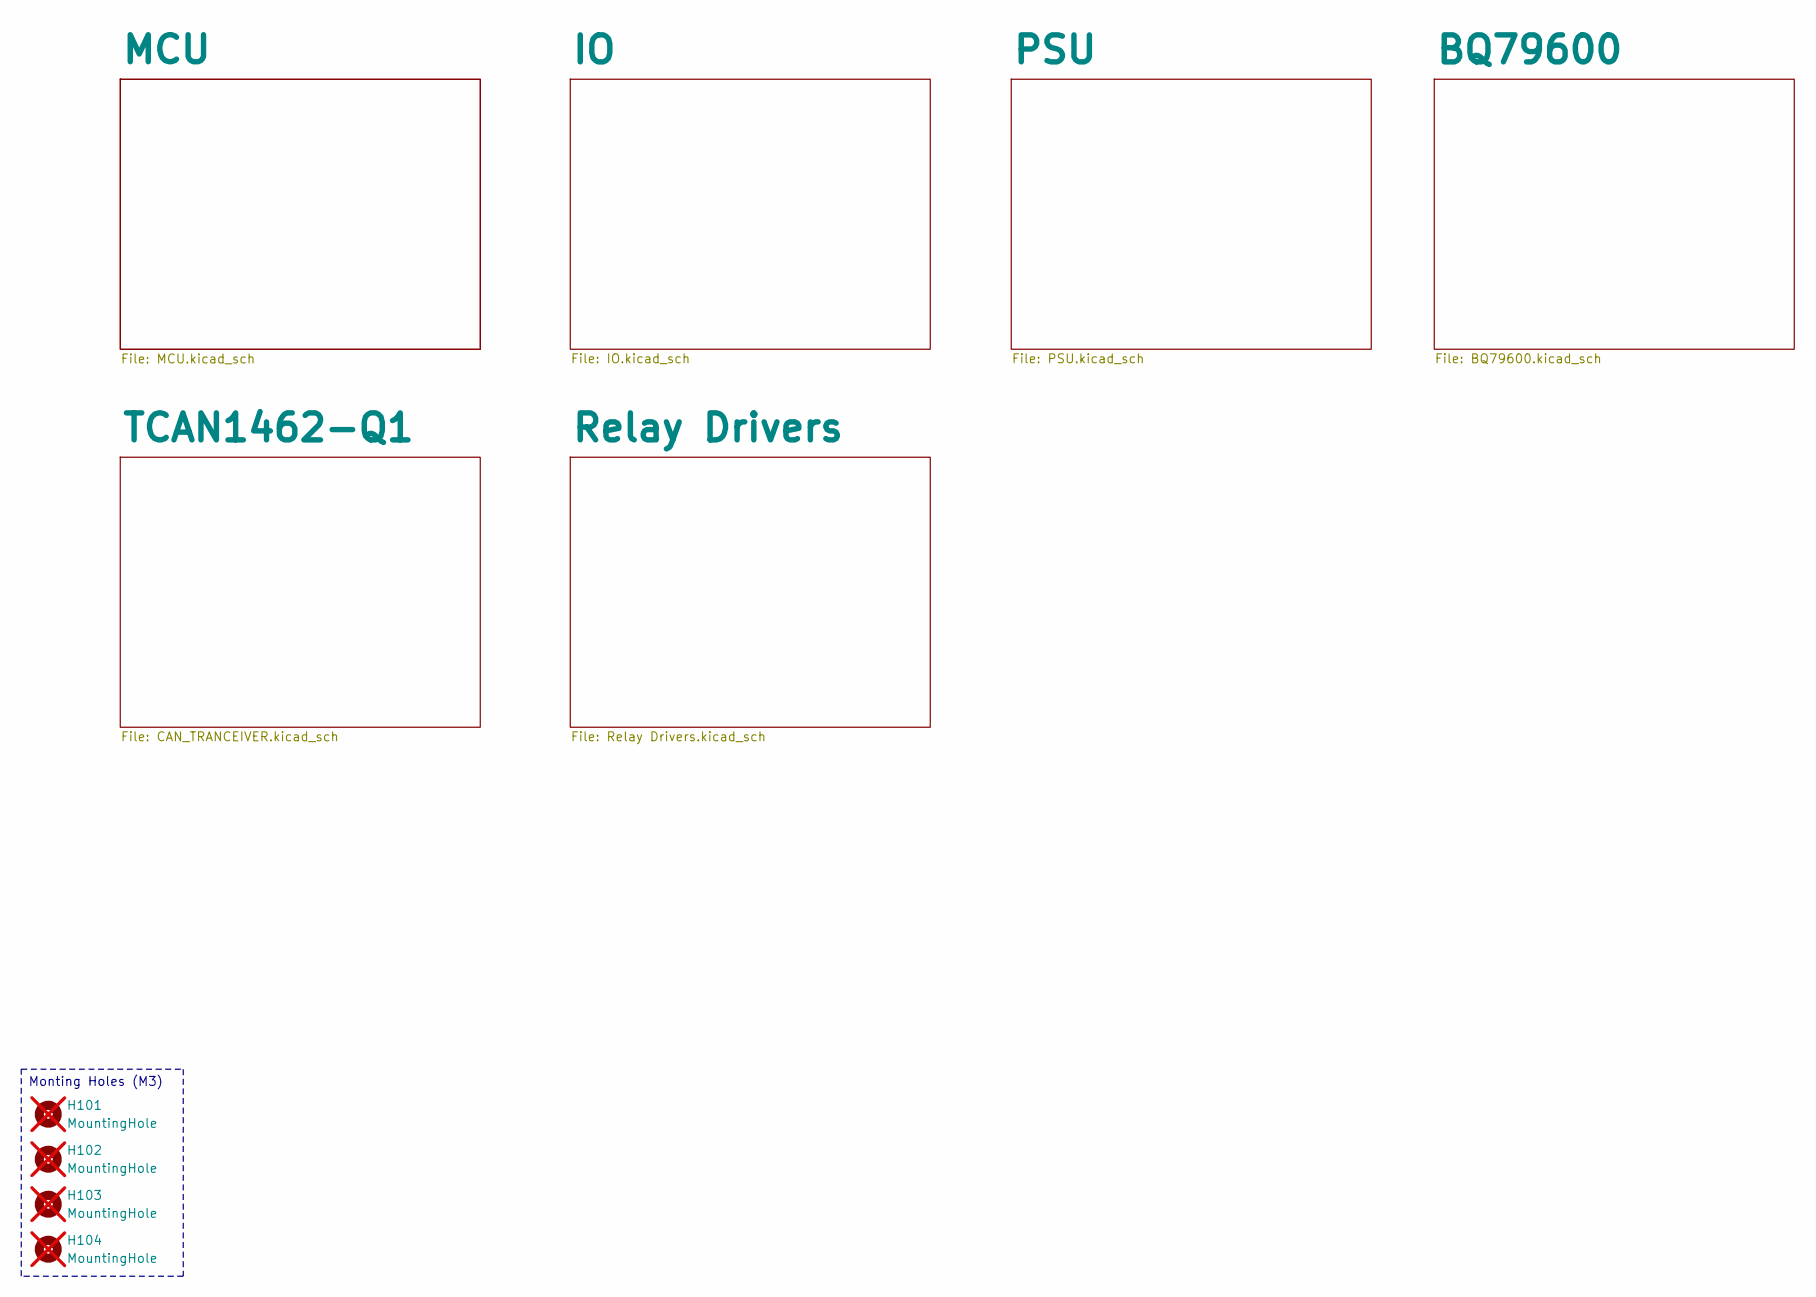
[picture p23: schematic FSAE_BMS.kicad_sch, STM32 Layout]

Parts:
H101, H102, H103, H104: MountingHole; MountingHole_3.2mm_M3; not fitted

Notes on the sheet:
Monting Holes (M3)

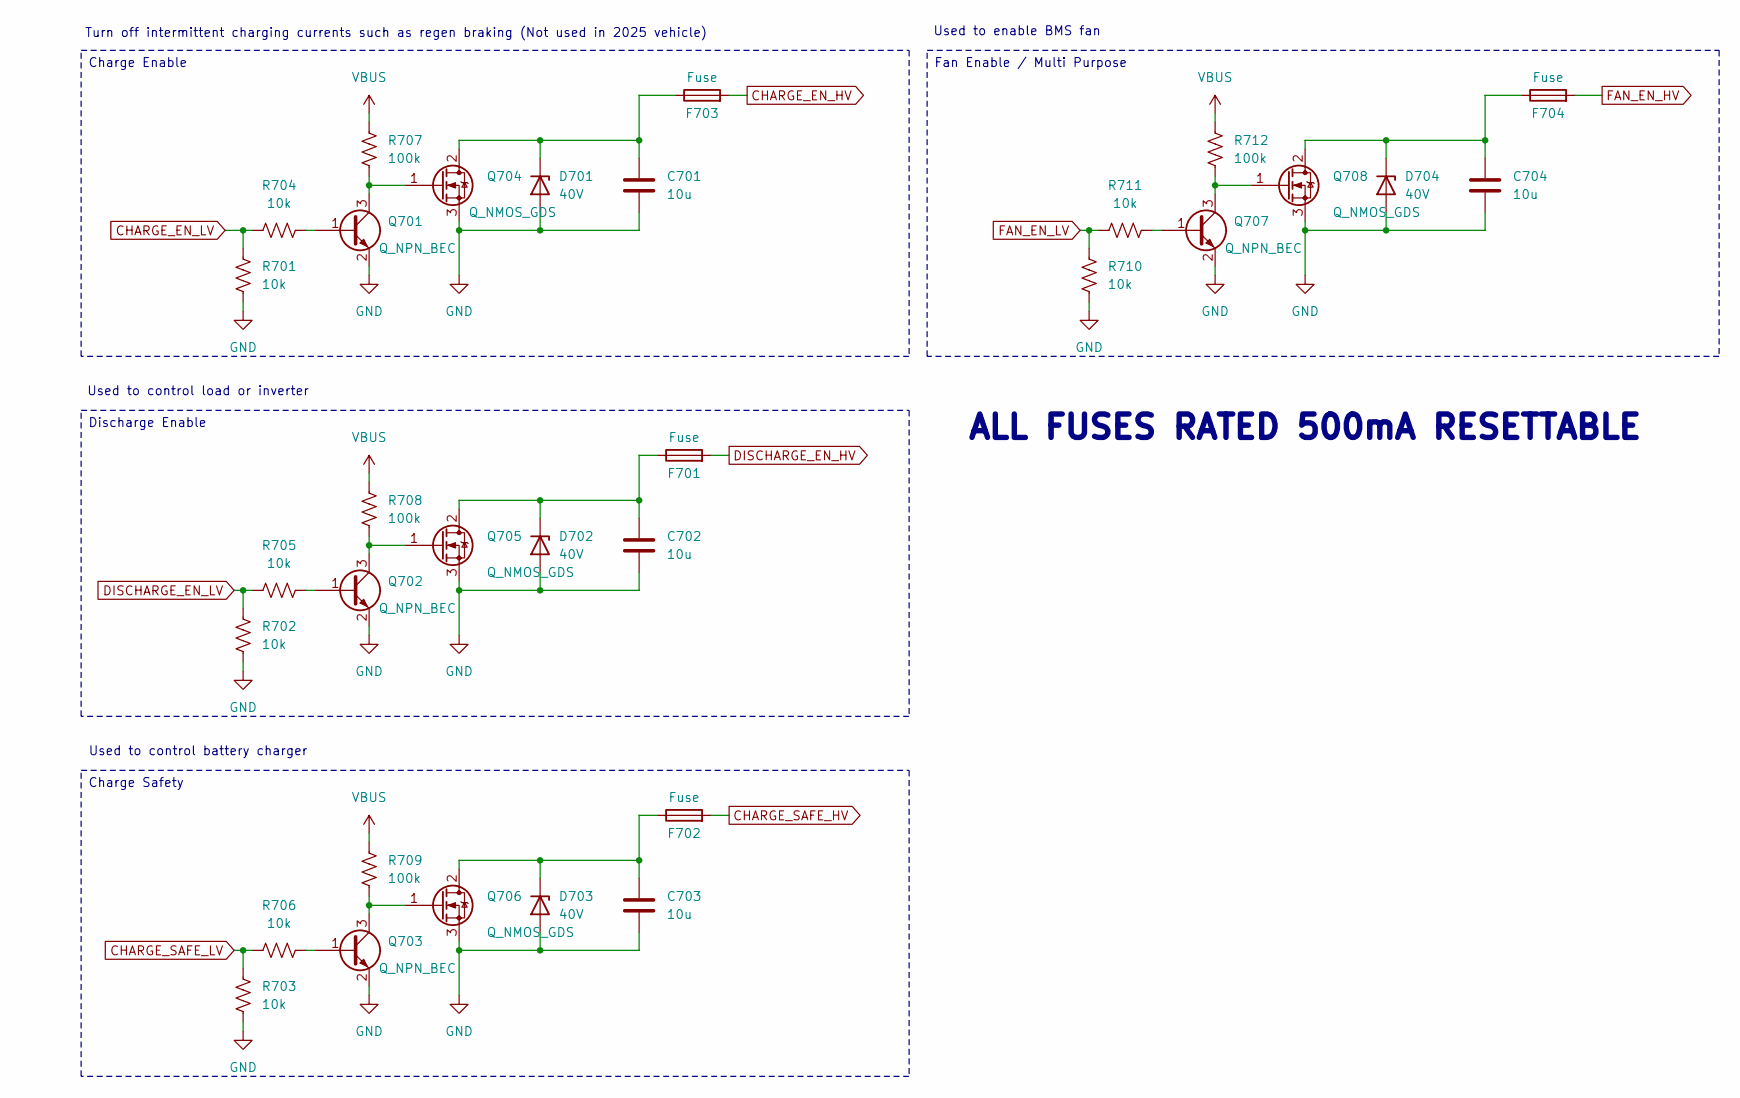
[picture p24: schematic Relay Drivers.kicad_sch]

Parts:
C701, C702, C703, C704: 10u; C_1206_3216Metric; Manufacturer_Part_Number CL31A106KBHNNNE; JLCPCB Part # C13585
D701, D702, D703, D704: 40V; D_SOD-123; Manufacturer_Part_Number BZT52C30; JLCPCB Part # C19077418
F701, F702, F703, F704: Fuse; Fuse_1812_4532Metric; Manufacturer_Part_Number SMD1812P050TF/30; JLCPCB Part # C12559
Q701, Q702, Q703, Q707: Q_NPN_BEC; SOT-23; Manufacturer_Part_Number MMBT3904; JLCPCB Part # C7420353
Q704, Q705, Q706, Q708: Q_NMOS_GDS; TO-263-2; Manufacturer_Part_Number IRF3205STRLPBF; JLCPCB Part # C2613
R701, R702, R703, R704, R705, R706, R710, R711: 10k; R_0402_1005Metric; Manufacturer_Part_Number FRC0603J103TS; JLCPCB Part # C2930027
R707, R708, R709, R712: 100k; R_0402_1005Metric; Manufacturer_Part_Number 0402WGF1003TCE; JLCPCB Part # C25741

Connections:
CHARGE_EN_HV: F703.2; also elsewhere on the board
CHARGE_EN_LV: R701.2, R704.1; also elsewhere on the board
CHARGE_SAFE_HV: F702.2; also elsewhere on the board
CHARGE_SAFE_LV: R703.2, R706.1; also elsewhere on the board
DISCHARGE_EN_HV: F701.2; also elsewhere on the board
DISCHARGE_EN_LV: R702.2, R705.1; also elsewhere on the board
FAN_EN_HV: F704.2; also elsewhere on the board
FAN_EN_LV: R710.2, R711.1; also elsewhere on the board
GND: C701.2, C702.2, C703.2, C704.2, D701.2 (A), D702.2 (A), D703.2 (A), D704.2 (A), Q701.2 (E), Q702.2 (E), Q703.2 (E), Q704.3 (S), Q705.3 (S), Q706.3 (S), Q707.2 (E), Q708.3 (S), R701.1, R702.1, R703.1, R710.1; also elsewhere on the board
unnamed: C701.1, D701.1 (K), F703.1, Q704.2 (D)
unnamed: C702.1, D702.1 (K), F701.1, Q705.2 (D)
unnamed: C703.1, D703.1 (K), F702.1, Q706.2 (D)
unnamed: C704.1, D704.1 (K), F704.1, Q708.2 (D)
unnamed: Q701.1 (B), R704.2
unnamed: Q701.3 (C), Q704.1 (G), R707.2
unnamed: Q702.1 (B), R705.2
unnamed: Q702.3 (C), Q705.1 (G), R708.2
unnamed: Q703.1 (B), R706.2
unnamed: Q703.3 (C), Q706.1 (G), R709.2
unnamed: Q707.1 (B), R711.2
unnamed: Q707.3 (C), Q708.1 (G), R712.2
VBUS: R707.1, R708.1, R709.1, R712.1; also elsewhere on the board

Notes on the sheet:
Turn off intermittent charging currents such as regen braking (Not used in 2025 vehicle)
Used to control load or inverter
ALL FUSES RATED 500mA RESETTABLE
Used to control battery charger
Used to enable BMS fan
Charge Safety
Fan Enable / Multi Purpose
Discharge Enable
Charge Enable

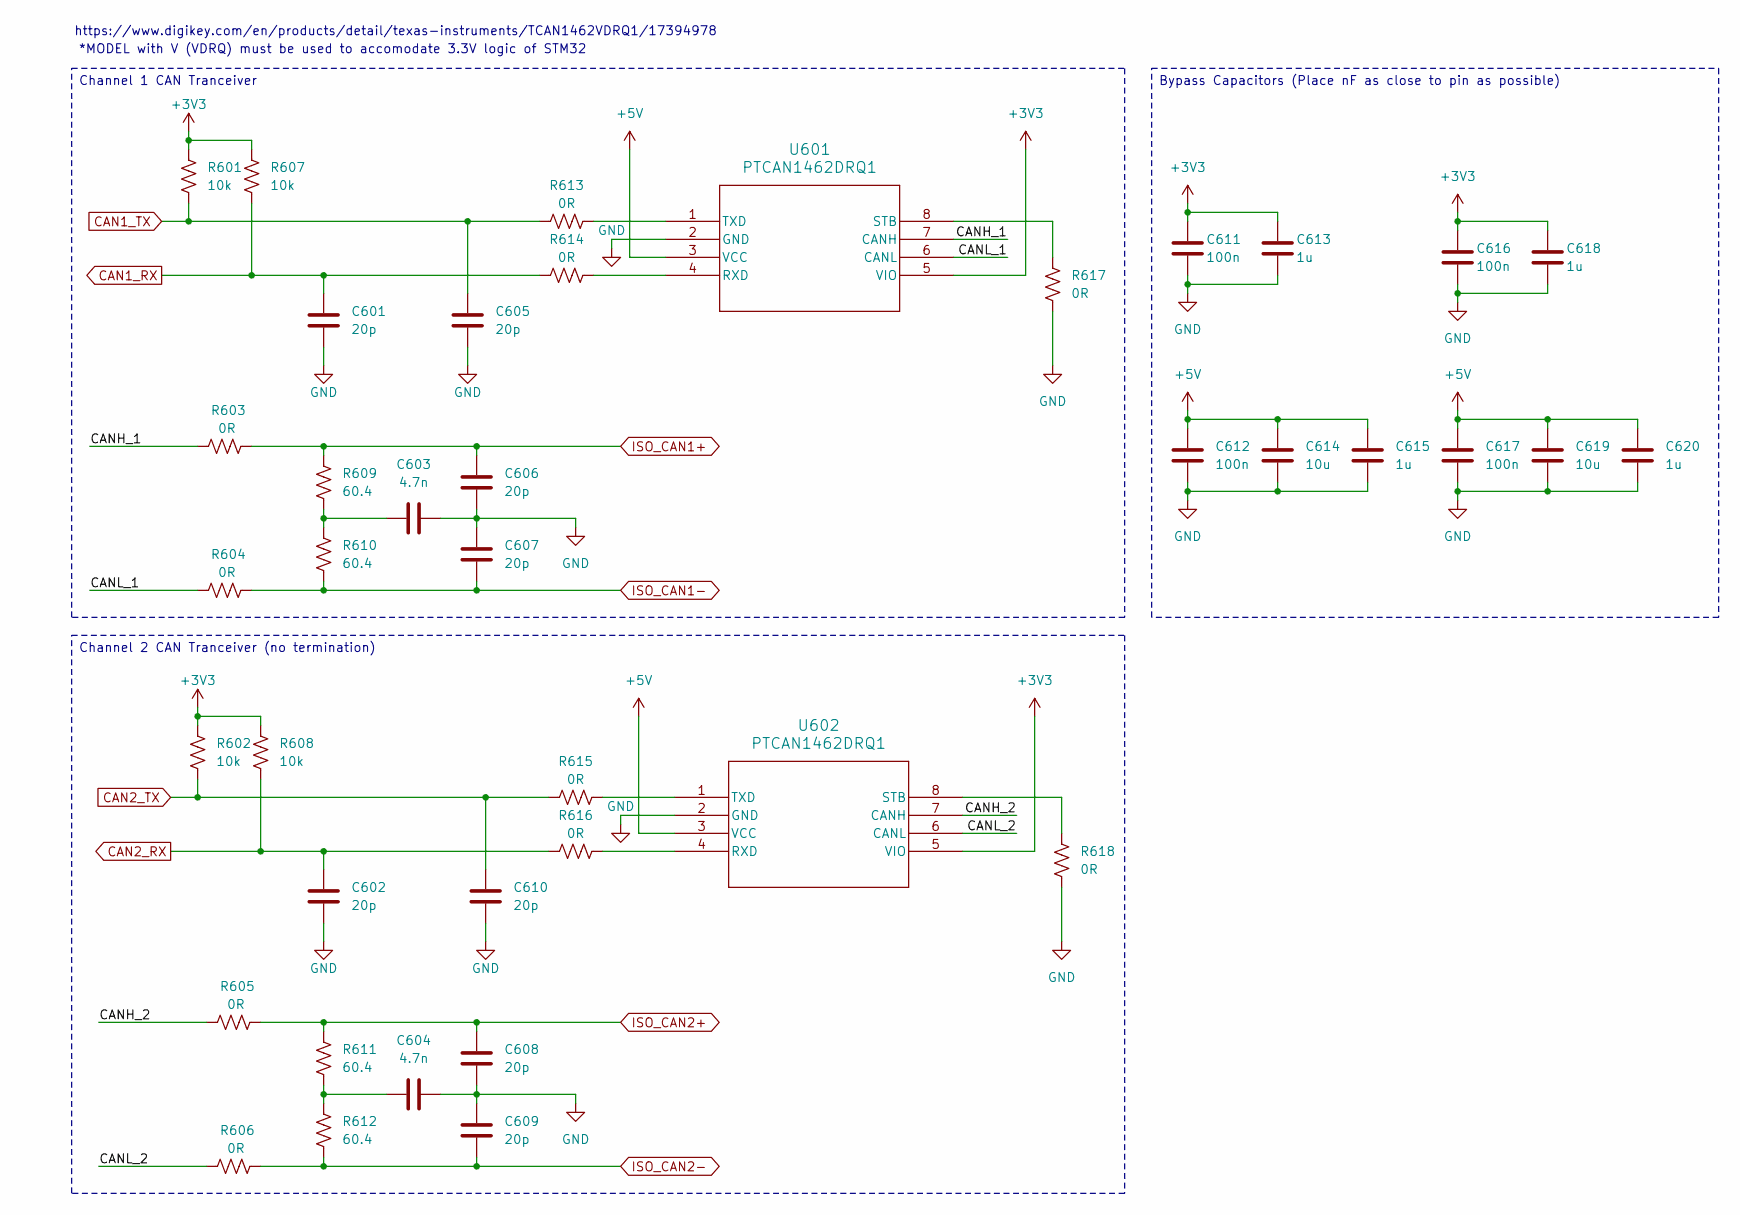
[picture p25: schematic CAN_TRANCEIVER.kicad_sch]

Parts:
C601, C602, C605, C606, C607, C608, C609, C610: 20p; C_0402_1005Metric; Manufacturer_Part_Number 0402CG200J500NT; JLCPCB Part # C1554
C603, C604: 4.7n; C_0402_1005Metric; Manufacturer_Part_Number CC0402JRX7R9BB472; JLCPCB Part # C281757
C611, C612, C616, C617: 100n; C_0402_1005Metric; Manufacturer_Part_Number CL05B104KO5NNNC; JLCPCB Part # C1525
C613, C615, C618, C620: 1u; C_0402_1005Metric; Manufacturer_Part_Number CL05A105KO5NNNC; JLCPCB Part # C29266
C614, C619: 10u; C_0603_1608Metric; Manufacturer_Part_Number CL10A106KP8NNNC; JLCPCB Part # C19702
R601, R602, R607, R608: 10k; R_0402_1005Metric; Manufacturer_Part_Number FRC0603J103TS; JLCPCB Part # C2930027
R603, R604, R605, R606: 0R; R_1206_3216Metric; Manufacturer_Part_Number HP06W2J0000T5E; JLCPCB Part # C473612
R609, R610, R611, R612: 60.4; R_1210_3225Metric; Manufacturer_Part_Number AC1210FR-0760R4L; JLCPCB Part # C230306
R613, R614, R615, R616, R617, R618: 0R; R_0805_2012Metric; Manufacturer_Part_Number 0805W8F0000T5E; JLCPCB Part # C17477
U601, U602: PTCAN1462DRQ1; CAN1462; Manufacturer_Part_Number TCAN1462VDRQ1; JLCPCB Part # C7399456

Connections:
+3V3: C611.1, C613.1, C616.1, C618.1, R601.1, R602.1, R607.1, R608.1, U601.5 (VIO), U602.5 (VIO); also elsewhere on the board
+5V: C612.1, C614.1, C615.1, C617.1, C619.1, C620.1, U601.3 (VCC), U602.3 (VCC); also elsewhere on the board
/TCAN1462-Q1/CANH_1: R603.1, U601.7 (CANH)
/TCAN1462-Q1/CANH_2: R605.1, U602.7 (CANH)
/TCAN1462-Q1/CANL_1: R604.1, U601.6 (CANL)
/TCAN1462-Q1/CANL_2: R606.1, U602.6 (CANL)
CAN1_RX: C601.2, R607.2, R614.1; also elsewhere on the board
CAN1_TX: C605.2, R601.2, R613.1; also elsewhere on the board
CAN2_RX: C602.2, R608.2, R616.1; also elsewhere on the board
CAN2_TX: C610.2, R602.2, R615.1; also elsewhere on the board
GND: C601.1, C602.1, C603.2, C604.2, C605.1, C606.1, C607.2, C608.1, C609.2, C610.1, C611.2, C612.2, C613.2, C614.2, C615.2, C616.2, C617.2, C618.2, C619.2, C620.2, R617.2, R618.2, U601.2 (GND), U602.2 (GND); also elsewhere on the board
ISO_CAN1+: C606.2, R603.2, R609.2; also elsewhere on the board
ISO_CAN1-: C607.1, R604.2, R610.1; also elsewhere on the board
ISO_CAN2+: C608.2, R605.2, R611.2; also elsewhere on the board
ISO_CAN2-: C609.1, R606.2, R612.1; also elsewhere on the board
unnamed: C603.1, R609.1, R610.2
unnamed: C604.1, R611.1, R612.2
unnamed: R614.2, U601.4 (RXD)
unnamed: R617.1, U601.8 (STB)
unnamed: R613.2, U601.1 (TXD)
unnamed: R616.2, U602.4 (RXD)
unnamed: R618.1, U602.8 (STB)
unnamed: R615.2, U602.1 (TXD)

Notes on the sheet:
https://www.digikey.com/en/products/detail/texas-instruments/TCAN1462VDRQ1/17394978
*MODEL with V (VDRQ) must be used to accomodate 3.3V logic of STM32
Channel 2 CAN Tranceiver (no termination)
Channel 1 CAN Tranceiver
Bypass Capacitors (Place nF as close to pin as possible)


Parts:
C201, C216: 10u; C_0603_1608Metric; Manufacturer_Part_Number CL10A106KP8NNNC; JLCPCB Part # C19702
C202, C205: 10p; C_0402_1005Metric; Manufacturer_Part_Number GRM1555C1H100FA01D; JLCPCB Part # C161520
C203, C204, C206, C208, C210, C213, C215: 100n; C_0402_1005Metric; Manufacturer_Part_Number CL05B104KO5NNNC; JLCPCB Part # C1525
C207, C209: 2u2; C_0603_1608Metric; Manufacturer_Part_Number 0603B225K250NT; JLCPCB Part # C99228
C211: 10n; C_0402_1005Metric; Manufacturer_Part_Number CC0402KRX7R9BB103; JLCPCB Part # C60133
C212, C214: 1u; C_0402_1005Metric; Manufacturer_Part_Number CL05A105KO5NNNC; JLCPCB Part # C29266
D201, D203, D204, D205, D206, D207, D208, D209: D_TVS; D_SOD-323; Manufacturer_Part_Number PESD3V3L1BA,115; JLCPCB Part # C51450
D202: GREEN; LED_0603_1608Metric; Manufacturer_Part_Number VLMTG1401-GS08; JLCPCB Part # C511604
J201: Conn_ARM_SWD_TagConnect_TC2030; Tag-Connect_TC2030-IDC-FP_2x03_P1.27mm_Vertical; not fitted
J202: DM3AT-SF-PEJM5_40_; SD_CARD; Mouser Part Number 798-DM3AT-SF-PEJM540
L201: 10n; L_0402_1005Metric; Manufacturer_Part_Number LQG15HN10NJ02D; JLCPCB Part # C21585
R201: 1k; R_0402_1005Metric; Manufacturer_Part_Number 0402WGF1001TCE; JLCPCB Part # C11702
R202, R208, R209, R212: 10k; R_0402_1005Metric; Manufacturer_Part_Number FRC0603J103TS; JLCPCB Part # C2930027
R203: 0R; R_0402_1005Metric; Manufacturer_Part_Number 0402WGF0000TCE; JLCPCB Part # C17168
R204, R205, R206, R207, R210: 22R; R_0402_1005Metric; Manufacturer_Part_Number 0402WGF220JTCE; JLCPCB Part # C25092
R211: 0R; R_2512_6332Metric; Manufacturer_Part_Number 25121WJ0000T4E; JLCPCB Part # C25469
U201: STM32F205RBTx; LQFP-64_10x10mm_P0.5mm; Manufacturer_Part_Number STM32F205RBT6; JLCPCB Part # C8364
Y201: 16 Mhz; Crystal_SMD_3225-4Pin_3.2x2.5mm; Manufacturer_Part_Number X322516MLB4SI; JLCPCB Part # C13738

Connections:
+3.3VP: C215.1, C216.1, D209.2 (A2), J202.4 (VDD), R211.2
+3V3: C201.1, C203.1, C204.1, C206.1, C208.1, C210.1, C214.1, D201.2 (A2), J201.1 (VCC), L201.2, R208.1, R209.1, R211.1, R212.1, U201.1 (VBAT), U201.19 (VDD), U201.32 (VDD), U201.48 (VDD), U201.64 (VDD); also elsewhere on the board
/MCU/BOOT0: R202.1, U201.60 (BOOT0)
/MCU/CONN_NRST: D206.2 (A2), J201.3 (~RESET), R204.1
/MCU/CONN_SWCLK: D205.2 (A2), J201.4 (SWCLK), R205.1
/MCU/CONN_SWDIO: D204.2 (A2), J201.2 (SWDIO), R206.1
/MCU/CONN_SWO: D203.2 (A2), J201.6 (SWO), R207.1
/MCU/HSE_IN: C202.1, U201.5 (PH0), Y201.1
/MCU/HSE_OUT: R203.2, U201.6 (PH1)
/MCU/NRST: C213.1, R204.2, U201.7 (NRST)
/MCU/SDIO_CK: R210.1, U201.53 (PC12)
/MCU/SDIO_CK_L: J202.5 (CLK), R210.2
/MCU/SDIO_CMD: D207.2 (A2), J202.3 (CMD), R208.2, U201.54 (PD2)
/MCU/SDIO_D0: D208.2 (A2), J202.7 (DAT0), R209.2, U201.39 (PC8)
/MCU/SDIO_DET: J202.CD1 (CARD_DETECT), R212.2, U201.50 (PA15)
/MCU/SWCLK: R205.2, U201.49 (PA14)
/MCU/SWDIO: R206.2, U201.46 (PA13)
/MCU/SWO: R207.2, U201.55 (PB3)
/MCU/TEST_LED: D202.2 (A), U201.10 (PC2)
/MCU/XTAL_IN: C205.1, R203.1, Y201.3
ADC_IN: U201.9 (PC1); also elsewhere on the board
BQ_NFAULT: U201.30 (PB11); also elsewhere on the board
BQ_SPI_RDY: U201.35 (PB14); also elsewhere on the board
CAN1_RX: U201.44 (PA11); also elsewhere on the board
CAN1_TX: U201.45 (PA12); also elsewhere on the board
CAN2_RX: U201.33 (PB12); also elsewhere on the board
CAN2_TX: U201.34 (PB13); also elsewhere on the board
CHARGE_EN_LV: U201.24 (PC4); also elsewhere on the board
CHARGE_PWR_LV_ISO: U201.27 (PB1); also elsewhere on the board
CHARGE_SAFE_LV: U201.26 (PB0); also elsewhere on the board
DISCHARGE_EN_LV: U201.25 (PC5); also elsewhere on the board
FAN_EN_LV: U201.29 (PB10); also elsewhere on the board
GND: C201.2, C202.2, C203.2, C204.2, C205.2, C206.2, C207.2, C208.2, C209.2, C210.2, C211.2, C212.2, C213.2, C214.2, C215.2, C216.2, D201.1 (A1), D203.1 (A1), D204.1 (A1), D205.1 (A1), D206.1 (A1), D207.1 (A1), D208.1 (A1), D209.1 (A1), J201.5 (GND), J202.6 (VSS), J202.MP1, J202.MP2, J202.MP3, J202.MP4, J202.MP5, R201.2, R202.2, U201.12 (VSSA), U201.18 (VSS), U201.63 (VSS), Y201.2, Y201.4; also elsewhere on the board
unnamed: D202.1 (K), R201.1
unnamed: C207.1, U201.31 (VCAP_1)
unnamed: C209.1, U201.47 (VCAP_2)
READY_PWR_LV_ISO: U201.28 (PB2); also elsewhere on the board
SPI1_NSS: U201.20 (PA4); also elsewhere on the board
SPI_MISO: U201.22 (PA6); also elsewhere on the board
SPI_MOSI: U201.23 (PA7); also elsewhere on the board
SPI_SCK: U201.21 (PA5); also elsewhere on the board
UART4_RX: U201.15 (PA1); also elsewhere on the board
UART4_TX: U201.14 (PA0); also elsewhere on the board
USART2_RX: U201.17 (PA3); also elsewhere on the board
USART2_TX: U201.16 (PA2); also elsewhere on the board
VDDA: C211.1, C212.1, L201.1, U201.13 (VDDA)

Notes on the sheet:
Crystal App Note: AN2867
https://www.mouser.com/ProductDetail/Hirose-Connector/DM3AT-SF-PEJM540?qs=0WLLhGLuJYzPvbo0KPPEoQ%3D%3D
120mA Max ~40mA Typ
< 2R ESR
CL=10pf ESR=80R
SD Card Connector
MCU - STM32F205
SWD Connector


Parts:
C501, C502: 10n; C_0402_1005Metric; Manufacturer_Part_Number CC0402KRX7R9BB103; JLCPCB Part # C60133
C503, C504, C505, C506: 100p; C_0402_1005Metric; Manufacturer_Part_Number 0402CG101J500NT; JLCPCB Part # C1546
C507, C513: 220n; C_0603_1608Metric; Manufacturer_Part_Number CL10B224KA8NNNC; JLCPCB Part # C21120
C508: 220n; C_0402_1005Metric; Manufacturer_Part_Number CL05A224KA5NNNC; JLCPCB Part # C47129
C509, C510, C511, C512: 2200p; C_0805_2012Metric; Manufacturer_Part_Number CL21C222JBFNNNE; JLCPCB Part # C28260
D501: RED; LED_0603_1608Metric; Manufacturer_Part_Number KT-0603R; JLCPCB Part # C2286
D502, D503, D504, D505: D_TVS; D_SOD-323; Manufacturer_Part_Number ESD5V0D3B-TP; JLCPCB Part # C668923
IC501: BQ79600PWRQ1; BQ79600; Mouser Part Number 595-BQ79600PWRQ1
L501, L502: WE-SLM; Manufacturer_Part_Number 744242471; JLCPCB Part # C488250
R501: 1k; R_0402_1005Metric; Manufacturer_Part_Number 0402WGF1001TCE; JLCPCB Part # C11702
R502, R503, R504, R505: 499; R_0603_1608Metric; Manufacturer_Part_Number 0603WAF4990T5E; JLCPCB Part # C23065
R506, R515: 100k; R_0402_1005Metric; Manufacturer_Part_Number 0402WGF1003TCE; JLCPCB Part # C25741
R507, R508, R509, R514: 10k; R_0402_1005Metric; Manufacturer_Part_Number FRC0603J103TS; JLCPCB Part # C2930027
R510, R511, R512, R513: 51; R_1206_3216Metric; Manufacturer_Part_Number 1206W4F510JT5E; JLCPCB Part # C18019
R516, R517, R518, R519, R524, R525, R526, R527: 0R; R_0805_2012Metric; Manufacturer_Part_Number 0805W8F0000T5E; JLCPCB Part # C17477
R520, R521, R522, R523: 0R; R_0805_2012Metric; Manufacturer_Part_Number 0805W8F0000T5E; not fitted

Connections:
+3V3: C508.1, IC501.3 (VIO), R501.1, R506.1, R507.1, R508.1, R514.1, R515.1; also elsewhere on the board
+5V: C513.1, IC501.14 (CVDD), IC501.15 (BAT), IC501.16 (INH); also elsewhere on the board
/BQ79600/COMHN: C504.1, IC501.12 (COMHN), R503.2, R511.1
/BQ79600/COMHP: C503.2, IC501.13 (COMHP), R502.1, R510.1
/BQ79600/COMLN: C505.2, IC501.11 (COMLN), R504.1, R512.1
/BQ79600/COMLP: C506.1, IC501.10 (COMLP), R505.2, R513.1
BQ_NFAULT: D501.1 (K), IC501.2 (NFAULT), R506.2; also elsewhere on the board
BQ_SPI_RDY: IC501.8 (NUART/SPI_(SPI_RDY)), R515.2; also elsewhere on the board
GND: C501.1, C502.1, C503.1, C504.2, C505.1, C506.2, C507.1, C508.2, C513.2, D502.1 (A1), D503.2 (A2), D504.1 (A1), D505.2 (A2), IC501.9 (GND), R509.2; also elsewhere on the board
ISO_COMHN: R525.2; also elsewhere on the board
ISO_COMHP: R524.2; also elsewhere on the board
ISO_COMLN: R526.2; also elsewhere on the board
ISO_COMLP: R527.2; also elsewhere on the board
unnamed: C501.2, R502.2, R503.1
unnamed: C502.2, R504.2, R505.1
unnamed: C509.1, L501.3, R520.1
unnamed: C509.2, R516.2
unnamed: C510.1, L501.4, R521.1
unnamed: C510.2, R517.2
unnamed: C511.1, L502.3, R522.1
unnamed: C511.2, R518.2
unnamed: C512.1, L502.4, R523.1
unnamed: C512.2, R519.2
unnamed: D501.2 (A), R501.2
unnamed: D502.2 (A2), R510.2, R516.1
unnamed: D503.1 (A1), R511.2, R517.1
unnamed: D504.2 (A2), R512.2, R518.1
unnamed: D505.1 (A1), R513.2, R519.1
unnamed: C507.2, IC501.1 (DVDD)
unnamed: L501.1, R521.2, R525.1
unnamed: L501.2, R520.2, R524.1
unnamed: L502.1, R523.2, R527.1
unnamed: L502.2, R522.2, R526.1
SPI1_NSS: IC501.7 (NCS), R514.2; also elsewhere on the board
SPI_MISO: IC501.5 (MISO/TX), R508.2; also elsewhere on the board
SPI_MOSI: IC501.4 (MOSI/RX), R507.2; also elsewhere on the board
SPI_SCK: IC501.6 (SCLK), R509.1; also elsewhere on the board

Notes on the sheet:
REFERENCE - https://www.ti.com/lit/ug/sluuc57b/sluuc57b.pdf?ts=1736343697268
BQ79600


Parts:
C301: 1u; C_0402_1005Metric; Manufacturer_Part_Number CL05A105KO5NNNC; JLCPCB Part # C29266
D301, D302, D303, D304, D305: D_TVS; D_SOD-323; Manufacturer_Part_Number PESD3V3L1BA,115; JLCPCB Part # C51450
F301, F302: Fuse; Fuse_0805_2012Metric; Manufacturer_Part_Number SMD0805B050TF; JLCPCB Part # C269104
J301, J302: Conn_01x04_Pin; PinHeader_1x04_P2.54mm_Vertical; not fitted
J303: 1376357-3; 13763573; Mouser Part Number 571-1376357-3; not fitted
J304, J305: 430450200; CON_430450200_MOL; not fitted
J306: Conn_01x02_Pin; PinHeader_1x02_P2.54mm_Vertical; not fitted
R301, R302, R303, R304: 22R; R_1206_3216Metric; Manufacturer_Part_Number FRC1206J220 TS; JLCPCB Part # C2907457
R305: 2.2k; R_1206_3216Metric; Manufacturer_Part_Number 1206W4J0222T5E; JLCPCB Part # C26038

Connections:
+5V: F301.1, F302.1; also elsewhere on the board
ADC_IN: C301.1, R305.2; also elsewhere on the board
CHARGE_EN_HV: J303.8; also elsewhere on the board
CHARGE_PWR: J303.3; also elsewhere on the board
CHARGE_SAFE_HV: J303.6; also elsewhere on the board
DISCHARGE_EN_HV: J303.7; also elsewhere on the board
FAN_EN_HV: J303.10; also elsewhere on the board
GND: C301.2, D301.1 (A1), D302.1 (A1), D303.1 (A1), D304.1 (A1), D305.1 (A1), J301.1, J302.1, J303.12, J306.1; also elsewhere on the board
ISO_CAN1+: J303.18; also elsewhere on the board
ISO_CAN1-: J303.19; also elsewhere on the board
ISO_CAN2+: J303.20; also elsewhere on the board
ISO_CAN2-: J303.21; also elsewhere on the board
ISO_COMHN: J304.2; also elsewhere on the board
ISO_COMHP: J304.1; also elsewhere on the board
ISO_COMLN: J305.2; also elsewhere on the board
ISO_COMLP: J305.1; also elsewhere on the board
unnamed: D301.2 (A2), J301.3, R302.1
unnamed: D302.2 (A2), J302.3, R304.1
unnamed: D303.2 (A2), J301.2, R301.1
unnamed: D304.2 (A2), J302.2, R303.1
unnamed: D305.2 (A2), J306.2, R305.1
unnamed: F301.2, J301.4
unnamed: F302.2, J302.4
READY_PWR: J303.2; also elsewhere on the board
UART4_RX: R302.2; also elsewhere on the board
UART4_TX: R301.2; also elsewhere on the board
USART2_RX: R304.2; also elsewhere on the board
USART2_TX: R303.2; also elsewhere on the board

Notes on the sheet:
UART4 Header
Main IO - Orion BMS 2
COML Molex Header
COMH Molex Header
ADC Header
USART1 Header

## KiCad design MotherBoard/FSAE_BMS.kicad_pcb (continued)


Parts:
C401, C402: 10n; C_0402_1005Metric; Manufacturer_Part_Number CC0402KRX7R9BB103; JLCPCB Part # C60133
C403, C404: 4.7u; C_1206_3216Metric; Manufacturer_Part_Number 1206B475K500NT; JLCPCB Part # C29823
C405, C406, C415, C416, C417, C418: 100n; C_0402_1005Metric; Manufacturer_Part_Number CL05B104KO5NNNC; JLCPCB Part # C1525
C407, C408: 100u; CP_Elec_6.3x5.8; Manufacturer_Part_Number EEEFT1V101AP; JLCPCB Part # C128464
C409, C410, C411, C412, C413, C414: 1u; C_0805_2012Metric; Manufacturer_Part_Number CL21B105KBFNNNE; JLCPCB Part # C28323
C419, C420, C421, C422, C423, C424: 22u; C_0805_2012Metric; Manufacturer_Part_Number CL21A226MAQNNNE; JLCPCB Part # C45783
D401, D402: D_Zener; D_SOD-323; Manufacturer_Part_Number LM3Z3V3T1G; JLCPCB Part # C46279
D403, D404, D407, D408: D_TVS; D_SOD-123; Manufacturer_Part_Number SMF12CA; JLCPCB Part # C353317
D405, D406: D_Schottky; D_SMA; Manufacturer_Part_Number SS54; JLCPCB Part # C22452
D409, D410: GREEN; LED_0603_1608Metric; Manufacturer_Part_Number VLMTG1401-GS08; JLCPCB Part # C511604
F401, F402: 3A; Fuse_1206_3216Metric; Manufacturer_Part_Number 12H1300C; JLCPCB Part # C182445
L401, L402: 1.2u; L_Chilisin_BMRA00050530; Manufacturer_Part_Number BMRA000505301R2MA1; JLCPCB Part # C5296375
L403, L404: 10u; L_Sunlord_MWSA0603S; Manufacturer_Part_Number MWSA0603S-100MT; JLCPCB Part # C132141
R401, R404: 33k; R_0402_1005Metric; Manufacturer_Part_Number 0402WGF3302TCE; JLCPCB Part # C25779
R402, R403, R405: 100k; R_0402_1005Metric; Manufacturer_Part_Number 0402WGF1003TCE; JLCPCB Part # C25741
R406, R408: 22.1k; R_0402_1005Metric; Manufacturer_Part_Number 0402WGF2212TCE; JLCPCB Part # C43473
R407: 162k; R_0402_1005Metric; Manufacturer_Part_Number FRC0402F1623TS; JLCPCB Part # C2998128
R409, R410: 1k; R_0402_1005Metric; Manufacturer_Part_Number 0402WGF1001TCE; JLCPCB Part # C11702
U401, U402: LMR51430; SOT-23-6; Manufacturer_Part_Number LMR51430YDDCR; JLCPCB Part # C5210749

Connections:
+3V3: C419.1, C421.1, C423.1, D409.2 (A), L403.2, R405.1; also elsewhere on the board
+5V: C420.1, C422.1, C424.1, D410.2 (A), L404.2, R407.1; also elsewhere on the board
/PSU/BUCK_FB_3V3: R405.2, R406.1, U401.4 (FB)
/PSU/BUCK_FB_5V: R407.2, R408.1, U402.4 (FB)
/PSU/BUCK_SW_3V3: C417.2, L403.1, U401.2 (SW)
/PSU/BUCK_SW_5V: C418.2, L404.1, U402.2 (SW)
/PSU/CBOOT_3V3: C417.1, U401.6 (CB)
/PSU/CBOOT_5V: C418.1, U402.6 (CB)
CHARGE_PWR: F402.1; also elsewhere on the board
CHARGE_PWR_LV_ISO: C402.1, D401.1 (K), R403.2, R404.1; also elsewhere on the board
GND: C401.2, C402.2, C403.2, C404.2, C405.2, C406.2, C407.2, C408.2, C409.2, C410.2, C411.2, C412.2, C413.2, C414.2, C415.2, C416.2, C419.2, C420.2, C421.2, C422.2, C423.2, C424.2, D401.2 (A), D402.2 (A), D403.1 (A1), D404.1 (A1), D407.1 (A1), D408.1 (A1), R401.2, R404.2, R406.2, R408.2, R409.2, R410.2, U401.1 (GND), U402.1 (GND); also elsewhere on the board
unnamed: D403.2 (A2), D405.2 (A), F401.2, R402.1
unnamed: D404.2 (A2), D406.2 (A), F402.2, R403.1
unnamed: C407.1, C409.1, C411.1, C413.1, C415.1, D407.2 (A2), L401.2, U401.3 (VIN), U401.5 (EN)
unnamed: C408.1, C410.1, C412.1, C414.1, C416.1, D408.2 (A2), L402.2, U402.3 (VIN), U402.5 (EN)
unnamed: D409.1 (K), R409.1
unnamed: D410.1 (K), R410.1
READY_PWR: F401.1; also elsewhere on the board
READY_PWR_LV_ISO: C401.1, D402.1 (K), R401.1, R402.2; also elsewhere on the board
VBUS: C403.1, C404.1, C405.1, C406.1, D405.1 (K), D406.1 (K), L401.1, L402.1; also elsewhere on the board

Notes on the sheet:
https://www.ti.com/product/LMR51430/part-details/LMR51430YDDCR https://www.digikey.com/en/products/detail/vishay-dale/IHLP6767DZER220M11/2533938
f(sw) = 1.1Mhz I(load) = 3A Max
ESR = 0R018
0R067
Both Regulators f(sw) = 1.1Mhz I(load) = 3A Max
SMA/DO-214AC package for good thermal characteristics
MCU Communication
3.3V and 5V Automotive Grade Switching Regulators


Board: 4 copper layers, 115.0 x 125.0 mm, 237 parts (0 on the bottom side), 129 nets.

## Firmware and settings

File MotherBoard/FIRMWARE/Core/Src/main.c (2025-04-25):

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
/* Includes ------------------------------------------------------------------*/
#include "main.h"

/* USER CODE BEGIN Includes */
#include <stdbool.h>
#include <string.h>
#include <stdio.h>
#include <bq79600.h>
/* USER CODE END Includes */

ADC_HandleTypeDef hadc1;

CAN_HandleTypeDef hcan1;
CAN_HandleTypeDef hcan2;

SD_HandleTypeDef hsd;

SPI_HandleTypeDef hspi1;

TIM_HandleTypeDef htim4;

UART_HandleTypeDef huart4;
UART_HandleTypeDef huart2;

void SystemClock_Config(void);
static void MX_GPIO_Init(void);
static void MX_CAN1_Init(void);
static void MX_CAN2_Init(void);
static void MX_SDIO_SD_Init(void);
static void MX_SPI1_Init(void);
static void MX_USART2_UART_Init(void);
static void MX_UART4_Init(void);
static void MX_ADC1_Init(void);
static void MX_TIM4_Init(void);

/* USER CODE BEGIN PFP */
void Delay_us(uint32_t us);
/* USER CODE END PFP */

/* USER CODE BEGIN 0 */
int _write(int file, char *ptr, int len){
  int i = 0;
  for(i = 0; i<len; i++)
    ITM_SendChar((*ptr++));
  return len;
}

/* USER CODE END 0 */

/**
  * @brief  The application entry point.
  * @retval int
  */
int main(void)
{
  /* USER CODE BEGIN 1 */
  HAL_StatusTypeDef status;
  /* USER CODE END 1 */

  /* MCU Configuration--------------------------------------------------------*/

  /* Reset of all peripherals, Initializes the Flash interface and the Systick. */
  HAL_Init();

  /* Configure the system clock */
  SystemClock_Config();

  /* Initialize all configured peripherals */
  MX_GPIO_Init();
  MX_CAN1_Init();
  MX_CAN2_Init();
  // MX_SDIO_SD_Init();
  MX_SPI1_Init();
  MX_USART2_UART_Init();
  MX_UART4_Init();
  MX_ADC1_Init();
  MX_TIM4_Init();

  /* USER CODE BEGIN 2 */
  HAL_CAN_Start(&hcan1);
  HAL_TIM_Base_Start(&htim4);

  printf("BQ79600 Battery Monitor System Starting...\r\n");

  // Step 2: Wake up and initialize the BQ79600 and BQ79616

  printf("Waking up BQ79600...\r\n");
  // wake is true if device went into shutdown mode
  bool wake = false;
  status = BQ79600_WakeUp(TOTALBOARDS,wake);
  if(status == HAL_OK){
	  printf("Wake GOOD\r\n");
  }

  //auto-address the stack
  printf("Auto-addressing...\r\n");
  status = SpiAutoAddress(TOTALBOARDS);
  if(status == HAL_OK){
  	  printf("Auto-addressing GOOD\r\n");
   }
  else
	  printf("HAL ERROR %d\r\n", status);


  printf("Initialization complete, starting main loop...\r\n");


  /*
  status = simpleBalancing();
  if(status == HAL_OK){
	  printf("BALANCING START GOOD\r\n");
  }
  else
	  printf("BALANCING START BAD %d\r\n", status);
	*/

  /* USER CODE END 2 */

  /* Infinite loop */
  /* USER CODE BEGIN WHILE */
  while (1)
  {

	//HAL_ADC_Start(&hadc1);
	//status = HAL_ADC_PollForConversion(&hadc1, 100);
	if (status == HAL_OK)
	{
	    // Read the ADC value
		//uint16_t adc_value = HAL_ADC_GetValue(&hadc1);

	    // Process the ADC value as needed
	    // For example, you might want to convert to voltage:
	    //float voltage5 = (adc_value * 3.3f) / 4095.0f;  // Assuming 3.3V reference and 12-bit resolution

		/*
	    printf("ADC READ %f \r\n", voltage5);
	    if(status == HAL_OK){
	    	printf("ADC READ GOOD\r\n");
	    	}
	    else
	    	printf("ADC ERROR %d\r\n", status);
	    	*/
	}


	status = stackVoltageRead(ACTIVECHANNELS);
	/*
	if(status == HAL_OK){
		printf("VOLTAGE READ GOOD\r\n");
	   }
	else
		printf("VOLTAGE READ ERROR %d\r\n", status);
	*/
	HAL_Delay(1000);

    /* USER CODE BEGIN 3 */

  }
  /* USER CODE END 3 */
}



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
/* USER CODE BEGIN 4 */
/**
 * @brief  Microsecond delay function using a timer
 * @param  us: Number of microseconds to delay
 * @retval None
 * @note   This is a placeholder - implement using a timer peripheral
 */
void Delay_us(uint32_t us)
{
	__HAL_TIM_SET_COUNTER(&htim4,0);  // set the counter value a 0
	while (__HAL_TIM_GET_COUNTER(&htim4) < us);  // wait for the counter to reach the us input in the parameter
}
/* USER CODE END 4 */
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


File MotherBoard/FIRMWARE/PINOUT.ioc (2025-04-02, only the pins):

Mcu.UserName=STM32F205RBTx
PA0-WKUP.Signal=UART4_TX
PA1.Signal=UART4_RX
PA11.Signal=CAN1_RX
PA12.Signal=CAN1_TX
PA13.Signal=SYS_JTMS-SWDIO
PA14.Signal=SYS_JTCK-SWCLK
PA15.GPIO_Label=SDIO_DET
PA15.Signal=GPIO_Input
PA2.Signal=USART2_TX
PA3.Signal=USART2_RX
PA4.Signal=SPI1_NSS
PA5.Signal=SPI1_SCK
PA6.Signal=SPI1_MISO
PA7.Signal=SPI1_MOSI
PB0.GPIO_Label=CHARGE_SAFE_LV
PB0.Signal=GPIO_Output
PB1.GPIO_Label=CHARGE_PWR_LV_ISO
PB1.Signal=GPIO_Input
PB10.GPIO_Label=FAN_EN_LV
PB10.Signal=GPIO_Output
PB11.GPIO_Label=BQ_NFAULT
PB11.Signal=GPIO_Input
PB12.Signal=CAN2_RX
PB13.Signal=CAN2_TX
PB14.GPIO_Label=BQ_SPI_RDY
PB14.Signal=GPIO_Input
PB2.GPIO_Label=READY_PWR_LV_ISO
PB2.Signal=GPIO_Input
PB3.Signal=SYS_JTDO-SWO
PC1.Signal=ADCx_IN11
PC12.Signal=SDIO_CK
PC2.Signal=GPIO_Output
PC4.GPIO_Label=CHARGE_EN_LV
PC4.Signal=GPIO_Output
PC5.GPIO_Label=DISCHARGE_EN_LV
PC5.Signal=GPIO_Output
PC8.Signal=SDIO_D0
PD2.Signal=SDIO_CMD
PH0-OSC_IN.Signal=RCC_OSC_IN
PH1-OSC_OUT.Signal=RCC_OSC_OUT

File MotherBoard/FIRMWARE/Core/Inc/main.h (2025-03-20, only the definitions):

#define CHARGE_EN_LV_Pin GPIO_PIN_4
#define CHARGE_EN_LV_GPIO_Port GPIOC
#define DISCHARGE_EN_LV_Pin GPIO_PIN_5
#define DISCHARGE_EN_LV_GPIO_Port GPIOC
#define CHARGE_SAFE_LV_Pin GPIO_PIN_0
#define CHARGE_SAFE_LV_GPIO_Port GPIOB
#define CHARGE_PWR_LV_ISO_Pin GPIO_PIN_1
#define CHARGE_PWR_LV_ISO_GPIO_Port GPIOB
#define READY_PWR_LV_ISO_Pin GPIO_PIN_2
#define READY_PWR_LV_ISO_GPIO_Port GPIOB
#define FAN_EN_LV_Pin GPIO_PIN_10
#define FAN_EN_LV_GPIO_Port GPIOB
#define BQ_NFAULT_Pin GPIO_PIN_11
#define BQ_NFAULT_GPIO_Port GPIOB
#define BQ_SPI_RDY_Pin GPIO_PIN_14
#define BQ_SPI_RDY_GPIO_Port GPIOB
#define SDIO_DET_Pin GPIO_PIN_15
#define SDIO_DET_GPIO_Port GPIOA

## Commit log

2024-09-29 Initial KiCAD Setup
    This is the initial project setup with an example of how to make the schematic design modular.
    [FSAE_BMS.kicad_pcb, FSAE_BMS.kicad_sch, MCU.kicad_sch]
2024-10-01 Initial daughter board setup
    [BQ79614_bootstrapping.kicad_sch, Project63_BMS_DaughterBoard.kicad_pcb, Project63_BMS_DaughterBoard.kicad_sch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]
2024-10-03 Initial MOBO Upload
    [FSAE_BMS.kicad_pcb, FSAE_BMS.kicad_sch, MCU.kicad_sch]
2024-10-10 Add files via upload
    Updated KiCAD schematics for Daughter Board. (10/10/24)
    [BQ79614_bootstrapping.kicad_sch, BatterytoBoard.kicad_sch, Project63_BMS_DaughterBoard.kicad_pcb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]
2024-10-15 Added IO and STM32 uC
    [1376357-3.stp, BQ79614_bootstrapping.kicad_sch, BatterytoBoard.kicad_sch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]
2024-10-15 Added IO Connector and uC
    [1376357-3.stp, FSAE_BMS.kicad_pcb, FSAE_BMS.kicad_sch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]
2024-10-17 Daughter_Board Update 2
    -Added some 3d models before fall break. (10/17/2024)
    [BQ79614_bootstrapping.kicad_sch, BatterytoBoard.kicad_sch, Project63_BMS_DaughterBoard.kicad_pcb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]
2024-10-17 DaughterBoard Update 2
    [705550019.stp, CAP_2012_TDK.step, CAP_GCM15_1p05X0p55X0p55_MUR.step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]
2024-10-27 modhy commit
    [BQ79614_bootstrapping.kicad_sch, NPN Power Supply.kicad_sch, Project63_BMS_DaughterBoard.kicad_pcb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]
2024-10-31 90% DOBO is done
    [5011.step, 5012.step, BQ79614_bootstrapping.kicad_sch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]
2024-11-02 NPN is done
    [EDI2CAP.CFG, G-31_MUR.step, NPN Power Supply.kicad_sch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]
2024-11-04 Complete bootstrap schematic for MCU
    [FSAE_BMS.kicad_pcb, FSAE_BMS.kicad_sch, IO.kicad_sch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]
2024-11-05 I think all componets for DOBO schematic are added, wired and assigned to their footprints. Next step to work on ERC
    [1.00kRC0603N_PAN.step, 1206J2K00222KXR.step, 744242471.PcbLib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]
2024-11-06 Test Commit
    [BQ79614_bootstrapping.kicad_sch, NPN Power Supply.kicad_sch, untitled.kicad_sch]
2024-11-07 Daughter Update
    [BQ79614_bootstrapping.kicad_sch, BatterytoBoard.kicad_sch, COMML.kicad_sch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]
2024-11-11 DOBO ERC 139 warnings left
    [COMML.kicad_sch, NPN Power Supply.kicad_sch, untitled.kicad_sch]
2024-11-15 PSU Complete
    [FSAE_BMS.kicad_pcb, IHLP6767DZ.step, IO.kicad_sch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]
2024-11-22 ready for pcb
    [705510038.stp, COMML.kicad_sch, Project63_BMS_DaughterBoard.kicad_pcb]
2024-11-23 only fuses left
    [BQ79614_bootstrapping.kicad_sch, COMML.kicad_sch]
2024-11-27 Starting Routing
    [Project63_BMS_DaughterBoard.kicad_pcb, untitled.kicad_sch]
2024-11-28 C:/Program Files/Git/
    [BQ79614_bootstrapping.kicad_sch, COMML.kicad_sch, NPN Power Supply.kicad_sch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]
2024-11-28 Layout continued. Fixed Footprint and most 3d model
    [744242471.PcbLib, 744242471.SchLib, 744242471.psm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]
2024-11-30 tracing left
    [BQ79614_bootstrapping.kicad_sch, BatterytoBoard.kicad_sch, COMML.kicad_sch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]
2024-12-11 Added BQ7900 rough draft and TCAN
    [BQ79600.kicad_sch, BQ79600PWRQ1.stp, CAN_TRANCEIVER.kicad_sch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]
2025-01-09 Fixed BQ79600 + minor changes
    [BQ79600.kicad_sch, CAN_TRANCEIVER.kicad_sch, DM3AT-SF-PEJM5_40_.SchLib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]
2025-01-10 Fixed CAN tranceivers + added relay driver circuit + fixed relative file paths for 3D models + finished PSU but still need correct 3D model
    [BQ79600.kicad_sch, CAN_TRANCEIVER.kicad_sch, FSAE_BMS.kicad_sch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]
2025-01-11 Revised all schematics + completed relay driver page
    [BQ79600.kicad_sch, CAN_TRANCEIVER.kicad_sch, FSAE_BMS.kicad_pcb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]
2025-01-13 Fixed 3D model paths. Finished PSU ORing shcematic.
    [430450200.stp, 5012.step, BQ79600.kicad_sch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]
2025-01-13 Added more 3D models
    [BQ79600.kicad_sch, CAN_TRANCEIVER.kicad_sch, FSAE_BMS.kicad_pcb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]
2025-01-17 Fixed relative paths + 90% footprints done + organized PCB for layout + found JLC part #s for manufacturing
    [BQ79600.kicad_sch, CAN_TRANCEIVER.kicad_sch, FSAE_BMS.kicad_pcb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]
2025-01-20 Initial Routing
    [BQ79614_bootstrapping.kicad_sch, Project63_BMS_DaughterBoard.kicad_pcb]
2025-01-20 Completed BOM except inductors
    [BQ79600.kicad_sch, CAN_TRANCEIVER.kicad_sch, FSAE_BMS.kicad_pcb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]
2025-01-21 Redesigned EMI filters for switching regulators to meet CISPR 25 Class 5 EMI constraint + substituted BOM #s for JLC basic parts
    [FSAE_BMS.kicad_pcb, FSAE_BMS.kicad_sch, PSU.kicad_sch]
2025-01-21 BOM completed + All 3D models added + Initial board shape complete
    [CAN_TRANCEIVER.kicad_sch, FSAE_BMS.kicad_pcb, IO.kicad_sch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]
2025-01-21 Routing update 2
    [Project63_BMS_DaughterBoard.kicad_pcb]
2025-01-26 Finished MCU + Tranceiver layout
    [FSAE_BMS.kicad_pcb, MCU.kicad_sch]
2025-01-27 Layout 90% complete
    [CAN_TRANCEIVER.kicad_sch, FSAE_BMS.kicad_pcb]
2025-01-28 Layout complete for regulators and relay drivers
    [FSAE_BMS.kicad_pcb]
2025-02-01 Routing Update 3
    [BQ79614_bootstrapping.kicad_sch, BatterytoBoard.kicad_sch, COMML.kicad_sch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]
2025-02-01 Finished layout need to route
    [3V3REG.kicad_sch, BQ79600.kicad_sch, BQ_MatchNet.kicad_sch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]
2025-02-03 Finished motherboard. Need to review BOM
    [BQ79600.kicad_sch, FSAE_BMS.kicad_pcb, IO.kicad_sch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]
2025-02-03 Fixed power routing mistake + finished BOM + generated manufacturing files
    [BOM.csv, BQ79600.kicad_sch, CAN_TRANCEIVER.kicad_sch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]
2025-02-04 Silkscreen edits
    [BQ79614_bootstrapping.kicad_sch, NPN Power Supply.kicad_sch, Project63_BMS_DaughterBoard.kicad_pcb]
2025-02-09 Reworked ground planes
    [Project63_BMS_DaughterBoard.kicad_pcb]
2025-02-10 Finished board
    [BQ79614_bootstrapping.kicad_sch, BatterytoBoard.kicad_sch, COMML.kicad_sch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]
2025-02-10 Daughterboard 100% Complete + Edited Motherboard BOM
    [BOM.csv, BQ79614_bootstrapping.kicad_sch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]
2025-02-10 Test-point silk screen edits complete
    [Project63_BMS_DaughterBoard.kicad_pcb]
2025-02-11 Both boards complete
    [BOM.csv, BQ79600.kicad_sch, BQ79614_bootstrapping.kicad_sch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]
2025-03-13 LED Blinky
2025-04-02 Initial BQ79600 -> BQ79616 communication
    [BQ79600.kicad_sch, CAN_TRANCEIVER.kicad_sch, FSAE_BMS.kicad_pcb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]
2025-04-15 Voltage reading function
2025-04-15 Updating SPI frame write function
2025-04-17 Fixes to voltage read - NOT WORKING
    [bq79600.c, main.c]
2025-04-17 voltage read working
2025-04-20 ADC Working
2025-04-22 Voltage stack read working + Vdelta calculation for balancing
    [Project63_BMS_DaughterBoard.kicad_pcb]

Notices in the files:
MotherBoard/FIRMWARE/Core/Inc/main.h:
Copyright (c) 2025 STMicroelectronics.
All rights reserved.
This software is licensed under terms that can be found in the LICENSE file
